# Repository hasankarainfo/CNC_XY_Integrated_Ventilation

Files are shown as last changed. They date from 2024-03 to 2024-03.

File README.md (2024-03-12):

# CNC_XY_Integrated_Ventilation
Diyot lazer uyumlu, bütünleşik havalandırmalı, iki eksen cnc.
<p align="center">
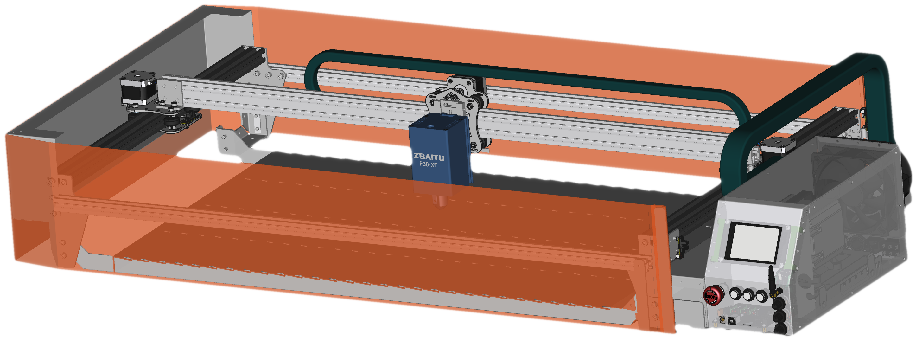
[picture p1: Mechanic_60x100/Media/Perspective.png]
    
</p>

Öne Çıkanlar:
1. Çalışması için, ihtiyaç duyduğu tüm materyalleri bütün olarak üzerinde barındırması,
2. Üzerinde bütünleşik bulunan ızgara ile, hava akımı yönlendirilmesi yanısıra, bal peteği ihtiyacının karşılanması,
3. Parça aydınlatma şiddeti, Havalandırma akış hızı, kompresör hava akış hız kontrolcüleri bulunması,
4. Tüm elektronik kontrolcülerin manuel ve ayrık yönetilmesi yanısıra, operasyonla birlikte de otomatik olarak bütünleşik çalışabilmesi,
5. Standart çalışma masası üzerinde, güç soketi ve havalandırma borusu takılmasına takriben kullanıma hazır olması,
6. Üretime uygunluğu ve mekanik dayanımı

Mekanik tasarımlar için FreeCad, Elektronik tasarımlar için ise Kicad, tamamen ücretsiz tasarım programları kullanılarak gerçekleştirildi.
<p align="left">
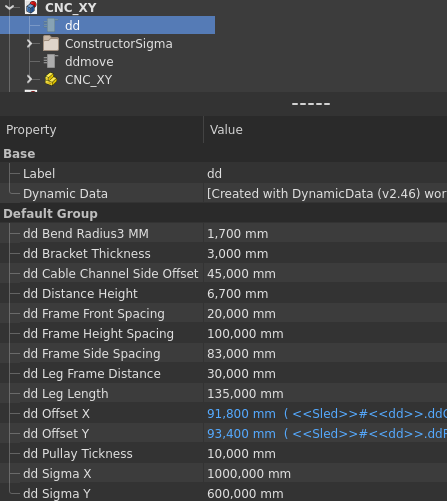
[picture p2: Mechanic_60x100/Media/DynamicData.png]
    
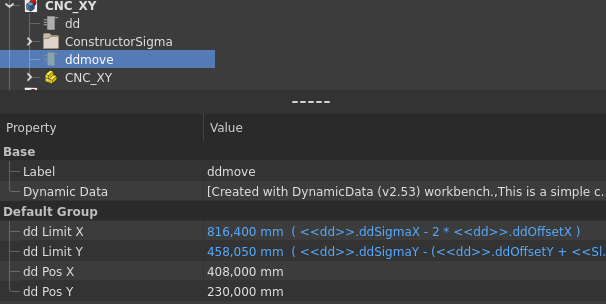
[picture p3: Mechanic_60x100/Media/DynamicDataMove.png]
    
</p>
CNC Mekanik boyutlar CNC_XY.FCStd dosyası ana sekmede dd (dynamic data) içerisinde ddSigmaX ve ddSigmaY değişkenleri üzerinden güncellenebilmektedir.
Bu değişkenler tasarımda bulunan x ve y eksenlerinde ki sigma profillerin birebir boylarına eştir. Sigma boylarına bağlı olan tüm parçalar otomatik güncellenecektir.
Bu durumda dikkat edilmesi gereken husus, büküm yapılacak metal parçalarda değişiklik meydana geldiğinge, üretime ilişkin  lazer kesim ve büküm rehberleri,
"./pr_.." dosyaları da ayrıca açılarak el ile güncellenmelidir. 3 boyutlu parçanın lazer kesime ve büküm rehberine uygunluğu için, 
yeniden "unfold" işlemi gerçekleştirilir. Yeniden meydana gelen kesim ve büküm eskiz'leri ilgili parçanın alanına sürüklenir. 
Teknik çizim dosyalarında, view sekmeleri içerisinde, ilişik olduğu eskiz ler, XSource properties üzerinden kesim ve büküm sıralaması ile güncellenir. 
Eski kesim ve büküm eskizleri silinebilir. Bazı durumda teknik çizimde ki ölçü belirteçleri de yeniden belirtilmesi gerekebilmektedir.

ddmove değişkenleri ile lazer hareket ettirilebilir. Sigma boyları ve diğer parametreler değerlendirilerek çalışma alanı otomatik hesaplanır, 
sonuç değerleri ddLimitX ddLimitY parametrelerinde görülür.

<p align="left">
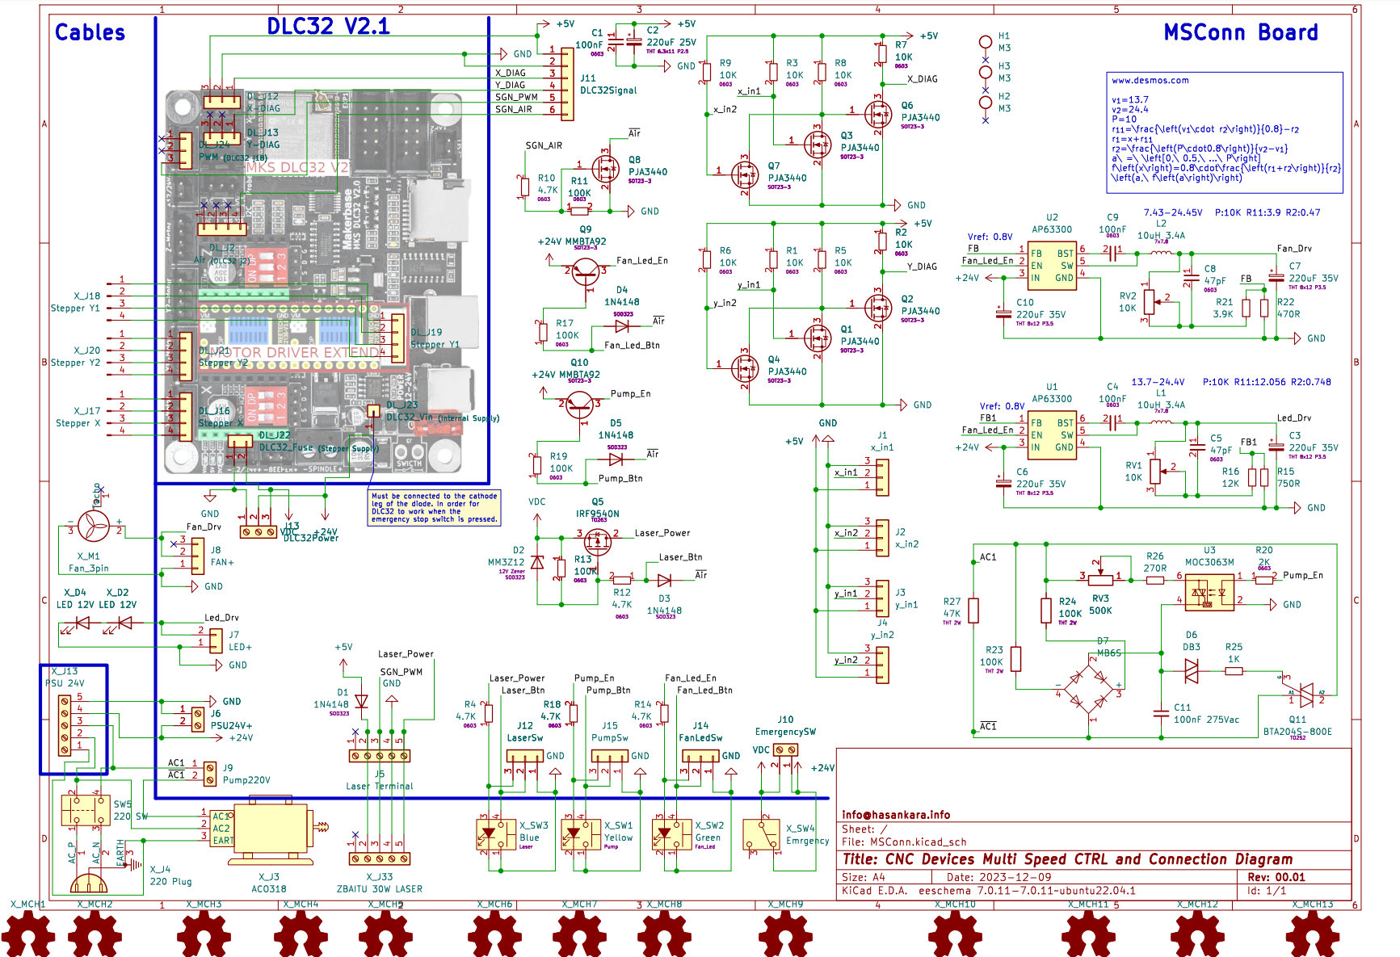
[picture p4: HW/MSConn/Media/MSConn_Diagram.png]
    
</p>
Elektriksel bağlantılar, Diyagram takip edilerek gerçekleştirilebilir. Diyagram MSConn board içerisinde tasarlandı, bu sayede kicad projesi üzerinden detaylı incelenebilir.
<p align="left">
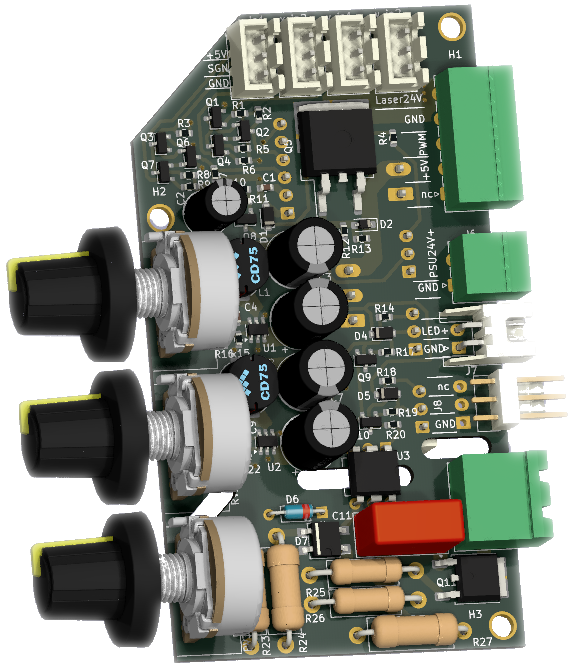
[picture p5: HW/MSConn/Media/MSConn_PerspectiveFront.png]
    
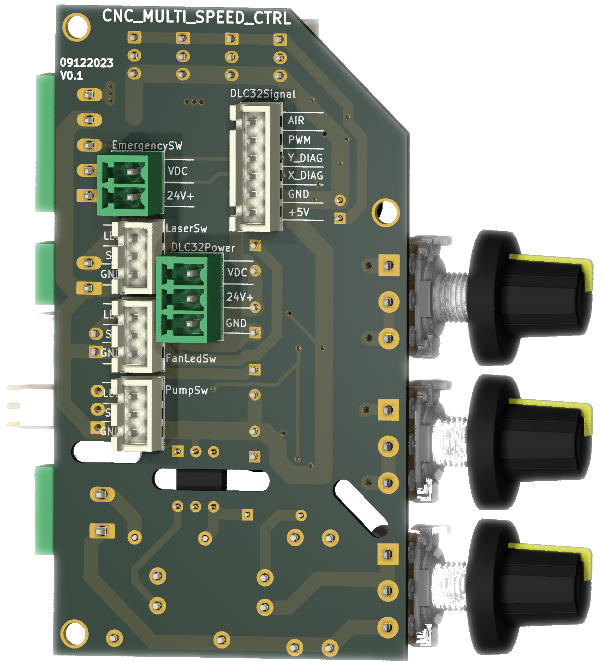
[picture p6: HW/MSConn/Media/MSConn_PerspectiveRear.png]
    
</p>

Üretim için öncelikle BOM dosyası incelenebilir.
Satın alınması gerekli materyallerin, satın alma linkleri ve yaklaşık fiyatlandırmaları Dolar cinsinde görülebilir.
1. sayfada genel toplam ve alt sayfaların sonuç fiyatlandırmaları görülmektedir.
2. sayfada Aygıt kutusu içerisinde kullanılan satın alınması gerekli parçalar görülmektedir.
3. sayfada satın alınması gerekli mekanik parçalar görülmektedir.
4. sayfada Projeye özgün metal parçaların üretilmesi için metal kesim, metal büküm listesi görülmektedir. 
    Dosya isimlerinden, metal kesimde kullanılacak materyalin cinsi ve kalınlığı anlaşılmaktadır.
    İhtiyaç duyulan kesim dosyaları, büküm rehberleri ve diş açma rehberleri "./Mechanic_60x100/Production_.." klasörlerinde bulunabilir.
5. sayfada "Multi Speed Controller and Connections" kartının üretiminde kullanılacak elektronik komponentlerin listesi bulunmaktadır.
    PCB üretiminde ihtiyaç duyulacak gerber dosyası "./HW/MSConn/FabOut_MSConn.zip" bulunabilir. 
    PCB Prototiplemede kullanılmak üzere detaylı MSConn bom listesi "./HW/MSConn/bom/ibom_MSConn.html"bulunabilir.
    Kart üzerinde konnektör pin isimleri anlamları ile birlikte yazmaktadır.

"./Mechanic_60x100/Media/" içerisinde ilk prototip montajına ilişkin fotoğraflar yer almaktadır. İlk prototip montaj esnasında,
görülen eksiklikler doğrultusunda, mekanik ve donanım tasarımlarında, gerekli görülen güncellemeler uygulanmıştır.

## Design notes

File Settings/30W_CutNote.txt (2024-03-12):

5mm mdf cut                         8mm focus 1 pass 250 speed, 100 power
5mm mdf, hardwood 45deg cut         8mm focus 1 pass 120 speed, 100 power
3mm translucent brown plexi cut     8mm focus 2 pass 220 speed, 100 power
3mm corrugated cardboard cutting    8mm focus 1 pass 4000 speed, 100 power

offset value 0.4mm. Used for complete overlap in cuts

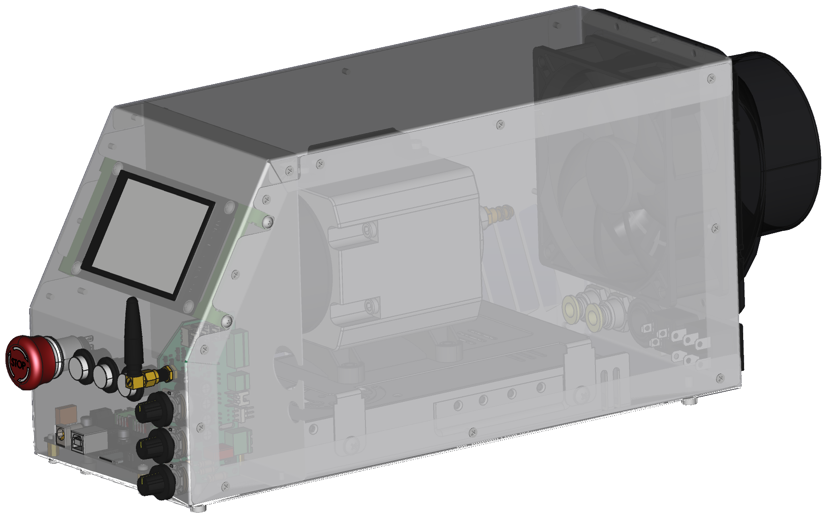
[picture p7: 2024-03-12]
Mechanic_60x100/Media/DevicesPerspective.png

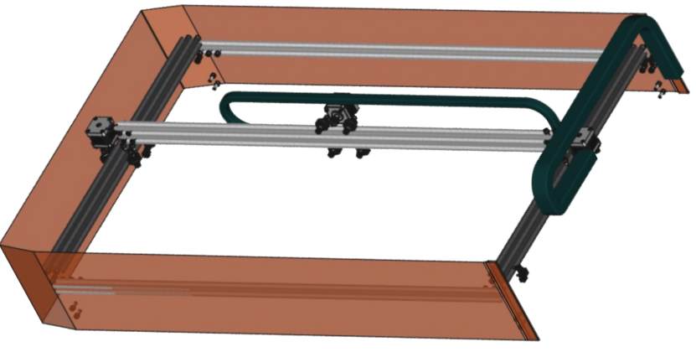
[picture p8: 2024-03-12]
Mechanic_60x100/Media/MechanicPerspective.png

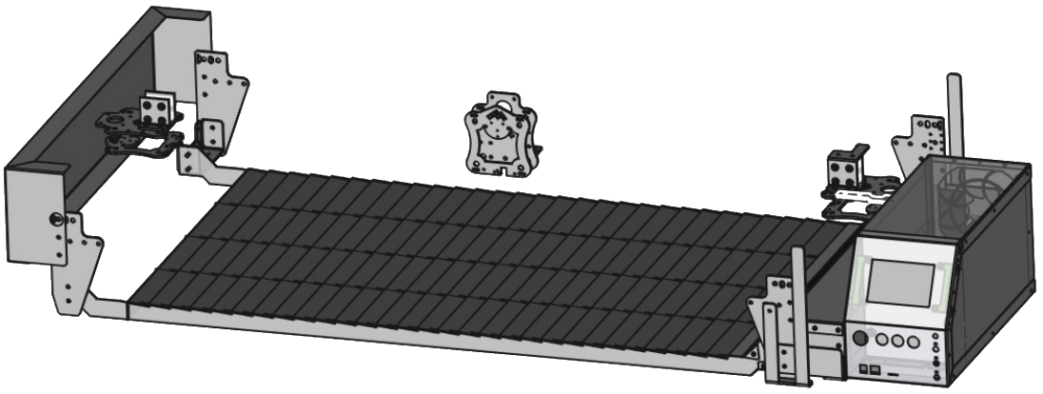
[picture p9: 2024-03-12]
Mechanic_60x100/Media/MetalProducedPerspective.png

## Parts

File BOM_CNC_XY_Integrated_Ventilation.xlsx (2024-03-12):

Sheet: Total
Reference | Value | Part Link | Part Number | Price | Qty
Laser | ZBAITU 30W LASER ~Price |  |  | 900 | 1 | 900.00
Devices Box Parts |  |  |  |  |  | 191.42
Mechanic Parts |  |  |  |  |  | 191.00
Metal Produced |  |  |  |  |  | 200.00
Grand Total |  |  |  |  |  | 1482.42

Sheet: Devices Box Parts
Reference | Value | Part Link | Part Number | Price | Qty
X_MCH7 | MKS DLC32 v2 | https://tr.aliexpress.com/item/1005005163045000.html | Suite 8 | 46 | 1 | 46.00
X_MCH8 | Air Flange 100mm | https://tr.aliexpress.com/item/1005005029283989.html | Color A | 6.7 | 1 | 6.70
X_MCH11 | Gland PG-13,5 | https://www.motorobit.com/pg-135-6-12-mm-polyamid-rakoru | OTO.SKP.02.000013 | 0.12 | 1 | 0.12
X_MCH12 | 2* Bulkhead Union 10mm | https://www.hidrofark.com/10-mm-perde-gecis-nipeli-pm-10 | PM-10 | 5 | 1 | 5.00
X_J3 | ACO318 | https://www.amazon.com.tr/gp/product/B00BNSQ16K/ref=ppx_yo_dt_b_asin_title_o00_s00 | ACO318 | 51 | 1 | 51.00
X_J4 | 220 Plug | https://www.motorobit.com/erkek-power-soketi-ic-212b | KOM.KNN.03.000014 | 0.25 | 1 | 0.25
X_J13 | PSU 24V | https://www.hatfon.com/urun/meanwell-lrs-350-24-350w-24v-14-6a-spms-guc-kaynagi | Lrs-350-24 | 35 | 1 | 35.00
X_M1 | Fan_3pin | https://www.perpaotomasyon.com/urun/krafe-120x120x38-24v-dc-turbo-fan | KF12038D24HB | 12 | 1 | 12.00
X_SW1 | Yellow | https://www.motorobit.com/rl16-503a-16mm-plastik-4-pin-kalici-buton-sari | BTN.PSH.01.000155 | 0.58 | 1 | 0.58
X_SW2 | Green | https://www.motorobit.com/rl16-503a-16mm-plastik-4-pin-kalici-buton-yesil | BTN.PSH.01.000154 | 0.58 | 1 | 0.58
X_SW3 | Blue | https://www.motorobit.com/rl16-503b-16mm-plastik-4-pin-yayli-buton-mavi | BTN.PSH.01.000161 | 0.58 | 1 | 12.00
X_SW4 | Emrgency | https://www.motorobit.com/19m-q1-19mm-metal-acil-stop-butonu | BTN.MTL.01.000419 | 6.8 | 1 | 11.60
SW5 | 220 SW | https://www.motorobit.com/kcd4-su-gecirmez-isikli-on-off-anahtar-4-pin | BTN.ROC.01.000020 | 1 | 1 | 0.01
MSConn |  |  |  |  |  | 10.58
Total |  |  |  |  |  | 191.42

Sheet: Mechanic Parts
Reference | Value | Part Link | Part Number | Price | Qty
X_D2, X_D4 | LED 12V + 12V |  | CT-4538 | 6.5 | 1 | 6.50
X_J17, X_J18, X_J20 | -- mixed values -- | https://www.rhino3dprinter.com/urun/nema-17-step-motor-nema17 | rhn-513249 | 11 | 3 | 33.00
X_MCH2 | 12x V Wheel | https://www.rhino3dprinter.com/urun/v-slot-tekerlek/239 | 47944814 | 12 | 1 | 12.00
X_MCH3 | 6x 6mm Eccentric Nut Group | https://www.rhino3dprinter.com/urun/eksantrik-somun/713 | RHN-511474 | 11.6 | 1 | 11.60
X_MCH4 | 3M Strap | https://www.rhino3dprinter.com/urun/kaliteli-gt2-6mm-kaucuk-kayis/4470 | RHN-523002 | 8.5 | 1 | 8.50
X_MCH5 | 3x GT2 Pulley 20Teeth | https://www.rhino3dprinter.com/urun/gt2-kasnak-20-dis-5mm/1096 | rhn-510705 | 2.8 | 1 | 2.80
X_MCH6 | 4x Optic Limit SW | https://www.motorobit.com/3d-yazici-optik-limit-switch-endstop | 3DP.3DE.01.000015 | 5 | 1 | 5.00
X_MCH9 | 102MM - 5 M PVC Air Duct | https://www.toprakvesu.com/afs-yirtilmaz-pvc-hava-kanali-102-mm | LB003 | 15.3 | 1 | 15.30
X_MCH10 | 3M Transparent Orange PVC Tarpaulin | https://www.kumasci.com/urun/seffaf-branda-pvc-mika-0,60-mm-turuncu-renkli-137-cm-en/5457 | KM-5457 | 21 | 1 | 21.00
X_MCH13 | 12mm 1M Cable Sock | https://www.rhino3dprinter.com/urun/12mm-siyah-kablo-corabi/3859 | RHN-514802 | 0.8 | 1 | 0.80
X_MCH14 | 1M 18x25 Cable Carrier | https://www.parsrulman.com/18x25-kablo-tasiyici-kapali/ | 18X25 | 10 | 1 | 10.00
X_MCH15 | 2M 10x10 Cable Carrier | https://www.parsrulman.com/10x10-kablo-tasiyici/ | 10x10 | 13 | 1 | 13.00
X_MCH16 | 2*60 1*100cm V_Sigma_40x20 | https://www.rhino3dprinter.com/urun/v-slot-20x40-siyah-sigma-profil | RHN-504520 | 33.5 | 1 | 33.50
X_MCH17 | 2*100cm Sigma_20x20 | https://www.rhino3dprinter.com/urun/sigma-profil-gri-renk-20x20 | RHN-516882 | 18 | 1 | 18.00
Total |  |  |  |  |  | 191.00

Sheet: Metal Produced
Reference | Part Link | Price
1.5mm aluminium cut
3mm aluminium cut
2mm Stainless steel cut
0.8mm Steel cut
2mm Steel cut
3mm Steel cut
Abkant Press Process
Mechanical Post Process
Total ~ |  |  | 200

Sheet: MSConn
Reference | Value | Pad | Part Link | Part Number | Price | Qty
C1, C4, C9 | 100nF | 603 | https://ozdisan.com/Product/Detail/476015/CC0603KRX7R9BB104 | CC0603KRX7R9BB104 | 0.006 | 3 | 0.02
C2 | 220uF 25V | THT 6.3x11 P2.5 | https://ozdisan.com/Product/Detail/404352/TMP221M1EE11M | TMP221M1EE11M | 0.06 | 1 | 0.06
C3, C6, C7, C10 | 220uF 35V | THT 8x12 P3.5 | https://ozdisan.com/Product/Detail/593553/JRB1V221M05000800120000A | JRB1V221M05000800120000A | 0.04 | 4 | 0.16
C5, C8 | 47pF | 603 | https://ozdisan.com/Product/Detail/747244/CC0603JRNPO9BN470 | CC0603JRNPO9BN470 | 0.006 | 2 | 0.01
C11 | 100nF 275Vac |  | https://ozdisan.com/Product/Detail/605274/W42Q3104KK6SD1A0W1 | W42Q3104KK6SD1A0W1 | 0.05 | 1 | 0.05
D1, D3-D5 | 1N4148 | SOD323 | https://ozdisan.com/Product/Detail/453557/1N4148WS-HT | 1N4148WS-HT | 0.014 | 4 | 0.06
D2 | MM3Z12 | SOD323 | https://ozdisan.com/Product/Detail/581368/MM3Z12-HT | MM3Z12-HT | 0.025 | 1 | 0.03
D6 | DB3 |  | https://www.ozdisan.com/Product/Detail/27193/DB3 | DB3 | 0.07 | 1 | 0.07
D7 | MB6S |  | https://ozdisan.com/Product/Detail/467250/MB6S-0-5A-HT | MB6S-0.5A-HT | 0.036 | 1 | 0.04
J1-J4, J12, J14, J15 | -- mixed values -- |  | https://www.ozdisan.com/Product/Detail/493781/DS1066-3MVW6X | DS1066-3MVW6X | 0.015 | 7 | 0.10
J5 | Laser Terminal |  | https://www.ozdisan.com/Product/Detail/353433/15EDGRC-3-5-05P-14-00SH | 15EDGRC-3.5-05P-14-00SH | 0.13 | 1 | 0.13
J6 | PSU24V+ |  | https://www.ozdisan.com/Product/Detail/424780/15EGTRC-3-5-02P-14-00AH | 15EGTRC-3.5-02P-14-00AH | 0.06 | 1 | 0.06
J7 | LED+ |  | https://www.ozdisan.com/Product/Detail/347995/DS1069-2MRW6SA | DS1069-2MRW6SA | 0.01 | 1 | 0.01
J8 | FAN+ |  | https://www.ozdisan.com/Product/Detail/458356/L-KLS1-2-54-03-R | L-KLS1-2.54-03-R | 0.03 | 1 | 0.03
J9 | Pump220V |  | https://www.ozdisan.com/Product/Detail/701614/2EGTRC-5-0-02P-14-00AH | 2EGTRC-5.0-02P-14-00AH | 0.06 | 1 | 0.06
J10 | EmergencySW |  | https://www.ozdisan.com/Product/Detail/707708/15EDGVC-3-5-02P-12-00AH | 15EDGVC-3.5-02P-12-00AH | 0.09 | 1 | 0.09
J11 | DLC32Signal |  | https://www.ozdisan.com/Product/Detail/348001/DS1069-6MVW6X | DS1069-6MVW6X | 0.03 | 1 | 0.03
J13 | DLC32Power |  | https://www.ozdisan.com/Product/Detail/701062/15EDGVC-3-5-03P-14-00AH | 15EDGVC-3.5-03P-14-00AH | 0.1 | 1 | 0.10
L1, L2 | 10uH 3.4A | 7x7.8 | https://ozdisan.com/Product/Detail/527917/FPI0705-100M | FPI0705-100M | 0.2 | 2 | 0.40
Q1-Q4, Q6-Q8 | PJA3440 | SOT23-3 | https://ozdisan.com/Product/Detail/517995/PJA3440R200001 | PJA3440_R2_00001 | 0.1 | 7 | 0.70
Q5 | IRF9540N | TO263 | https://ozdisan.com/Product/Detail/612326/IRF9540NSTRLPBF | IRF9540NSTRLPBF | 0.9 | 1 | 0.90
Q9, Q10 | MMBTA92 | SOT23-3 | https://ozdisan.com/Product/Detail/433898/MMBTA92-HT | MMBTA92-HT | 0.03 | 2 | 0.06
Q11 | BTA204S-800E | TO252 | https://ozdisan.com/Product/Detail/981895/BTA204S-800E118 | BTA204S-800E,118 | 0.34 | 1 | 0.34
R1-R3, R5-R9 | 10K | 603 | https://ozdisan.com/Product/Detail/341790/0603SAF1002T5E | 0603SAF1002T5E | 0.0015 | 8 | 0.01
R4, R10, R12, R14, R18 | 4.7K | 603 | https://ozdisan.com/Product/Detail/341796/0603SAF4701T5E | 0603SAF4701T5E | 0.0015 | 5 | 0.01
R11, R13, R17, R19 | 100K | 603 | https://ozdisan.com/Product/Detail/339374/0603SAF1003T5E | 0603SAF1003T5E | 0.0015 | 4 | 0.01
R15 | 750R |  | https://ozdisan.com/Product/Detail/344357/0603SAF7500T5E | 0603SAF7500T5E | 0.001 | 1 | 0.001
R16 | 12K |  | https://ozdisan.com/Product/Detail/353308/0603SAF1202T5E | 0603SAF1202T5E | 0.001 | 1 | 0.001
R20 | 2K | 603 | https://ozdisan.com/Product/Detail/347334/0603SAF2001T5E | 0603SAF2001T5E | 0.0015 | 1 | 0.0015
R21 | 3.9K |  | https://ozdisan.com/Product/Detail/357181/0603SAF3901T5E | 0603SAF3901T5E | 0.001 | 1 | 0.001
R22 | 470R |  | https://ozdisan.com/Product/Detail/348835/0603SAF4700T5E | 0603SAF4700T5E | 0.001 | 1 | 0.001
R23, R24 | 100K | THT 2W | https://www.ozdisan.com/Product/Detail/866960/CFR2WSJT-52-100K | CFR2WSJT-52-100K | 0.05 | 2 | 0.10
R25 | 1K |  | https://www.ozdisan.com/Product/Detail/904507/MFR-25FTE52-1K | MFR-25FTE52-1K | 0.015 | 1 | 0.01
R26 | 270R |  | https://www.ozdisan.com/Product/Detail/905436/MFR-25FTF52-270R | MFR-25FTF52-270R | 0.015 | 1 | 0.01
R27 | 47K | THT 2W | https://www.ozdisan.com/Product/Detail/867440/CFR3WSJT-73-47K | CFR3WSJT-73-47K | 0.06 | 1 | 0.06
RV1, RV2 | 10K |  | https://www.entegredunyasi.com.tr/urun/10k-mavi-potans | WH0162-10K POTANS | 0.84 | 2 | 1.68
RV3 | 500K |  | https://www.entegredunyasi.com.tr/urun/500k-mavi-potansiyometre-wh0162-500k | WH0162-500K POTANS | 0.84 | 1 | 0.84
U1, U2 | AP63300 |  | https://www.digikey.com/en/products/detail/diodes-incorporated/AP63300WU-7/10491510 | 31-AP63300WU-7CT-ND | 0.82 | 2 | 1.64
U3 | MOC3063M |  | https://ozdisan.com/Product/Detail/337684/MOC3063M | MOC3063M | 0.7 | 1 | 0.70
X_MCH1 | PCB Produced |  | https://jlcpcb.com/ |  | 2 | 1 | 2.00
 |  |  |  |  |  |  | 0.00
Total |  |  |  |  |  |  | 10.58

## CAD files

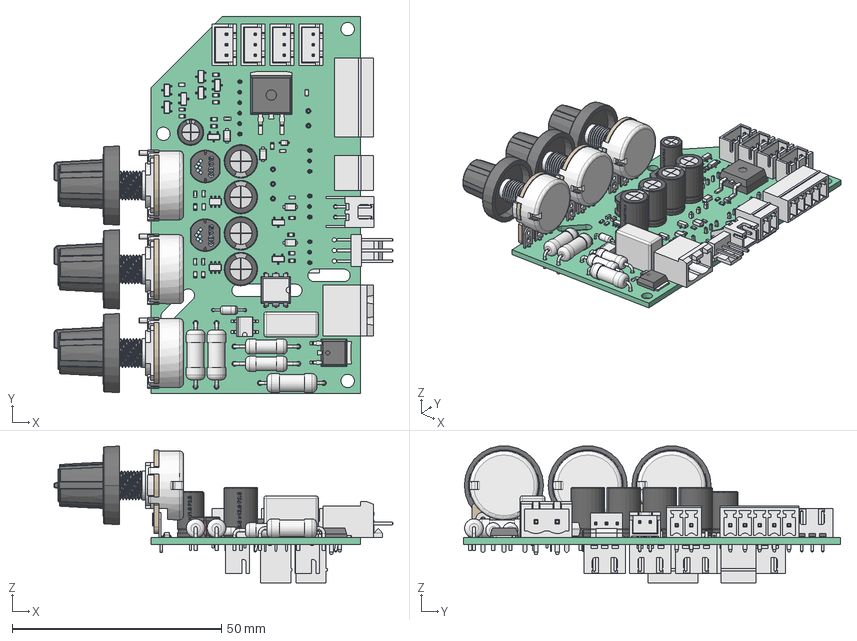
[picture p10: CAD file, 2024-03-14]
HW/MSConn/MSConn3D.FCStd
80.9 x 90.0 x 32.7 mm
Pcb_38e4
Knob_18.5 x 3
Mil x 3
pcb x 3
Pin3 x 3
Pin1 x 3
Pin2 x 3
Metal x 3
Q11_SOT_23_d14ee1c078b6 x 9
D7_D_SOD_323_dd79eabc5d6b
R15_R_0603_1608Metric_0c346f64d96a x 20
Sketch_On_Surface x 4
Sketch_On_Surface001 x 4
Sketch_On_Surface002 x 4
Sketch_On_Surface003 x 4
Sketch_On_Surface004 x 4
Sketch_On_Surface005 x 4
Sketch_On_Surface006 x 4
Sketch_On_Surface007 x 4
Sketch_On_Surface008 x 4
Sketch_On_Surface009 x 4
Sketch_On_Surface010 x 4
Sketch_On_Surface011 x 4
D8_TO-269AA_2bfa4c3bc879
C20_C_Rect_L130mm_W60mm_P1000mm_FKS3_FKP3_MKS4_719aee594432
D3_D_SOD_123F_0e6f75c736fe x 4
J15_JST_B3B_XH_A_ce7ef635c6d0 x 7
J29_MSTBA_01x02_G_5_08mm_e88b5a3cc893
C3_C_0603_1608Metric_60dfc148ec75 x 5
U5_TSOT_23_6_e728020bdb3d x 2
R22_R_Axial_DIN0414_L119mm_D45mm_P1524mm_Horizontal_7fed01040269 x 3
U6_DIP-6_W7.62mm_bc15a999cf1c
TextSolid x 2
TextSolid001 x 2
TextSolid002 x 2
TextSolid003 x 2
TextSolid004 x 2
TextSolid005 x 2
TextSolid006 x 2
TextSolid007 x 2
TextSolid008 x 2
TextSolid009 x 2
Pinouts_Fillet x 2
Pinouts_Fillet001 x 2
J27_JST_S2B_XH_A_f3c9ba6d6086
J31_MC_01x02_G_3_5mm_9bf914f047c8
J28_MC_01x05_G_3_5mm_ab80e944cf0b
J1_Fan_Pin_Header_Straight_1x03_85ed5d203a81
a3dd6ad7-9c39-11ed-93f0-dde97e994e83_part
a3dd6ad8-9c39-11ed-93f0-dde97e994e83_part
a3dd6ad9-9c39-11ed-93f0-dde97e994e83_part
a3dd6ad9-9c39-11ed-93f0-dde97e994e83_part001
a3dd6ad9-9c39-11ed-93f0-dde97e994e83_part002
R31_R_Axial_DIN0411_L99mm_D36mm_P1524mm_Horizontal_5a3f2440dadf x 2
Sketch_On_Surface013
Sketch_On_Surface014
Sketch_On_Surface015
Sketch_On_Surface016
Sketch_On_Surface017
Sketch_On_Surface018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

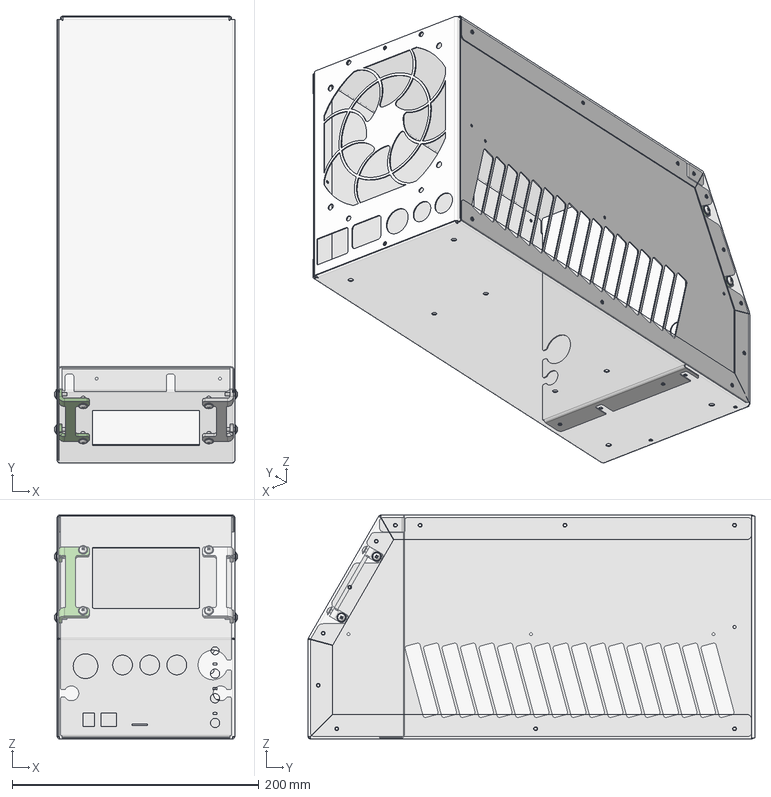
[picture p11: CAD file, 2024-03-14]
Mechanic_60x100/CNC_Devices.FCStd
148.8 x 362.4 x 181.6 mm
tft_screws_l x 2
tft_screws_local_l x 2
Fold
Frame_Side_L
Frame_Side_R
Frame_Rear
FrameSeperator
Frame_Main

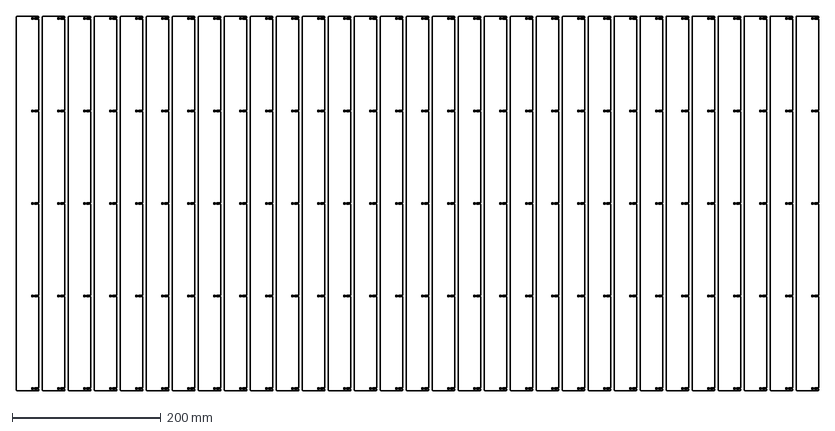
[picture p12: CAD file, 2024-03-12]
Mechanic_60x100/Production_LaserCut_Bending/Pr_Alu_1_5MM_LaserCut.dxf
1080.0 x 504.0 mm

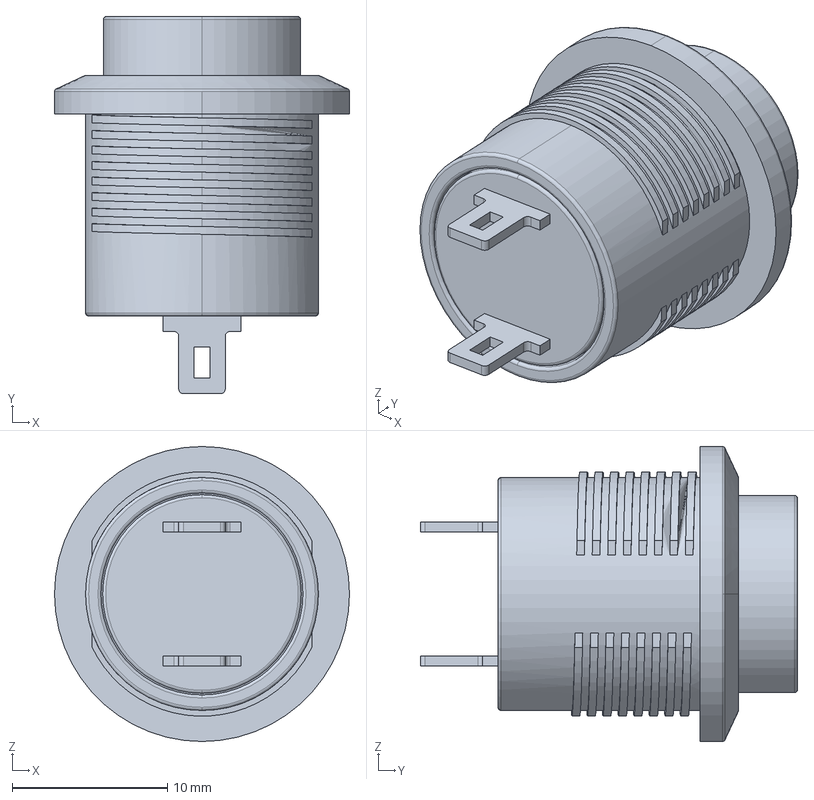
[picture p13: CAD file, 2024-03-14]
Mechanic_60x100/SubParts/Push_Button_D16.FCStd
19.0 x 24.3 x 19.0 mm

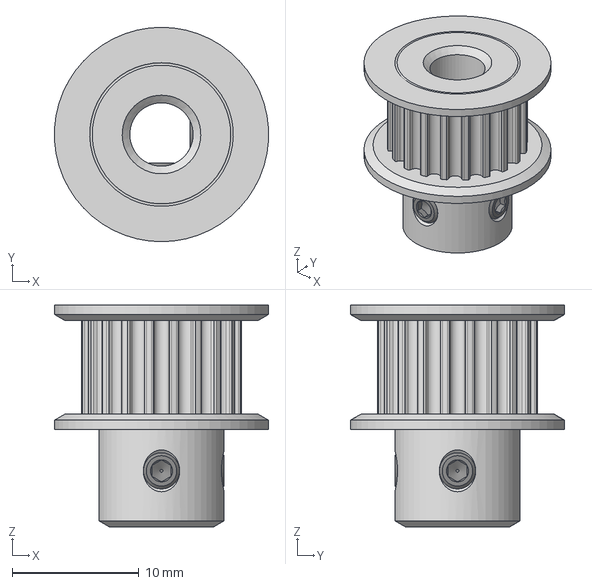
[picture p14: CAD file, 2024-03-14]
Mechanic_60x100/SubParts/Sled_SubParts/Pulley_GT_P.FCStd
16.9 x 16.9 x 17.5 mm
M3x2.6950000000000003-Screw x 2
CompoundFilter

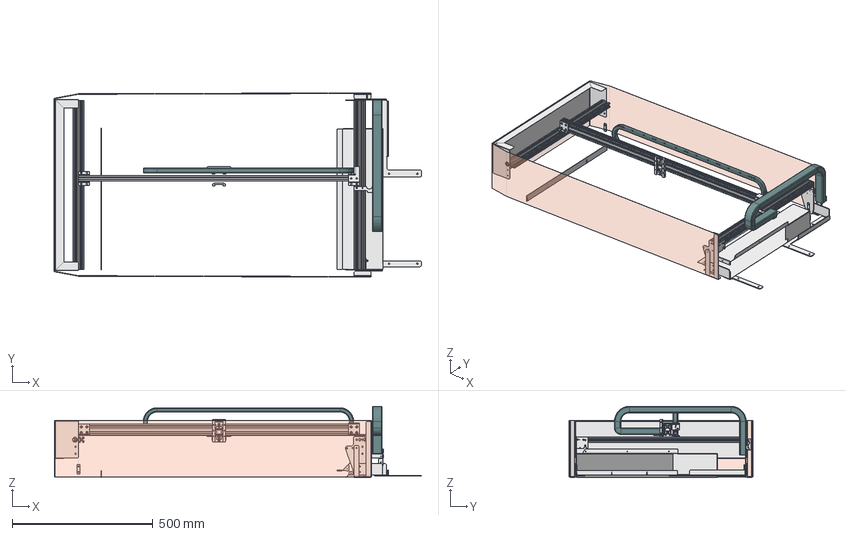
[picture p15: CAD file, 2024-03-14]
Mechanic_60x100/CNC_XY.FCStd
1305.3 x 653.5 x 253.6 mm
LaserElevator
SigmaMid4020
CompoundFilter003 x 4
CableChannelR
ExtrudeCableChannelSideHolder x 2
Slice009.0
SideGuard_
SigmaSide4020 x 2
TnutDouble x 2
LeftLimit
AirFrameTop
AirFrameBottom
CableChannelSidePlastic
Slice007.0
SensorMountF
M3x6xx5-Standoff
M3x6xx5-Standoff414
BaseBarrier
BaseBarrierHolderFront
BaseBarrierHolderRear
DeviceHolderF
DeviceHolderR
LegBaseRightFront
LegBaseRightRear

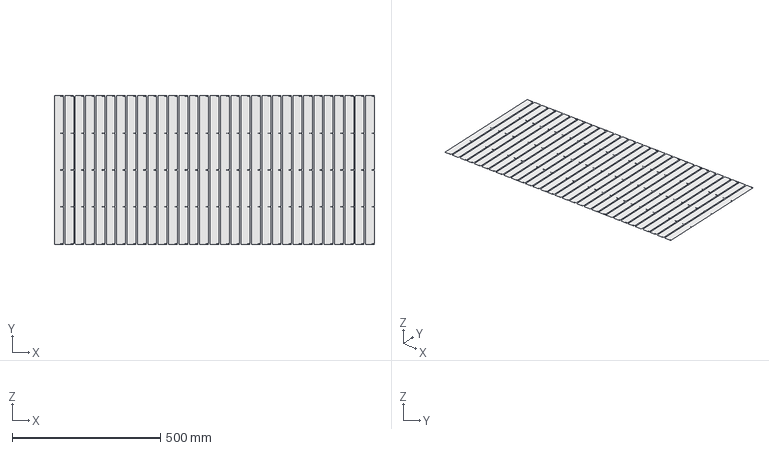
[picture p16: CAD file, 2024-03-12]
Mechanic_60x100/Production_LaserCut_Bending/Pr_Alu_1_5mm.FCStd
1080.0 x 504.0 x 0 mm

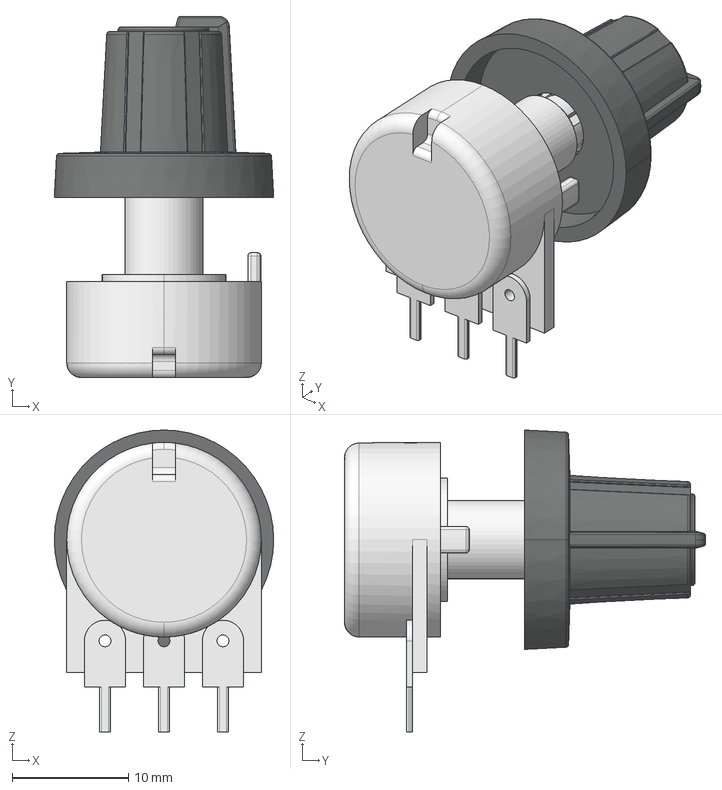
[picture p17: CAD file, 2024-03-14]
Mechanic_60x100/SubParts/Potentiometer_Mono.FCStd
18.9 x 31.1 x 26.0 mm
Knob_18.5
Potentiometer

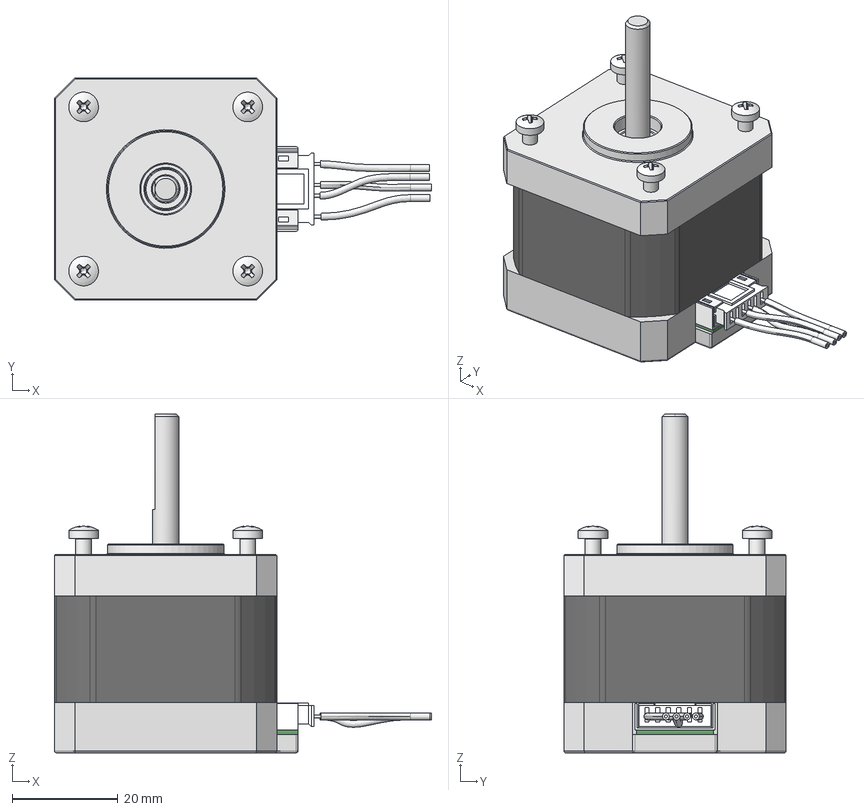
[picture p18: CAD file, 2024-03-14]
Mechanic_60x100/SubParts/Sled_SubParts/Nema_17HS4401_P.FCStd
71.2 x 42.0 x 64.0 mm
Axis&Rotor
BallBearing1
Stator_
Baseplate_
BallBearing1_
Seperate
PCB
ConnectorPins
ConnBase
Cables_Plastic
Cables_Cu_
Housing_Female__
FrontPlate
ScrewsBody
ScrewsAssembly

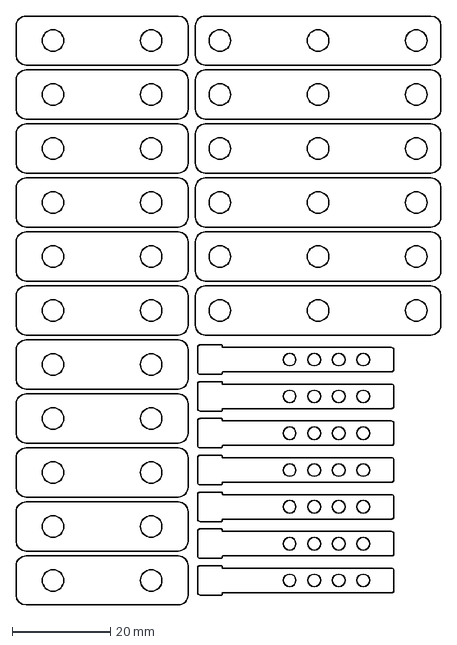
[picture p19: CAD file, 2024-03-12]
Mechanic_60x100/Production_LaserCut_Bending/Pr_StainlessSteel_2MM_LaserCut.DXF
86.5 x 120.0 mm

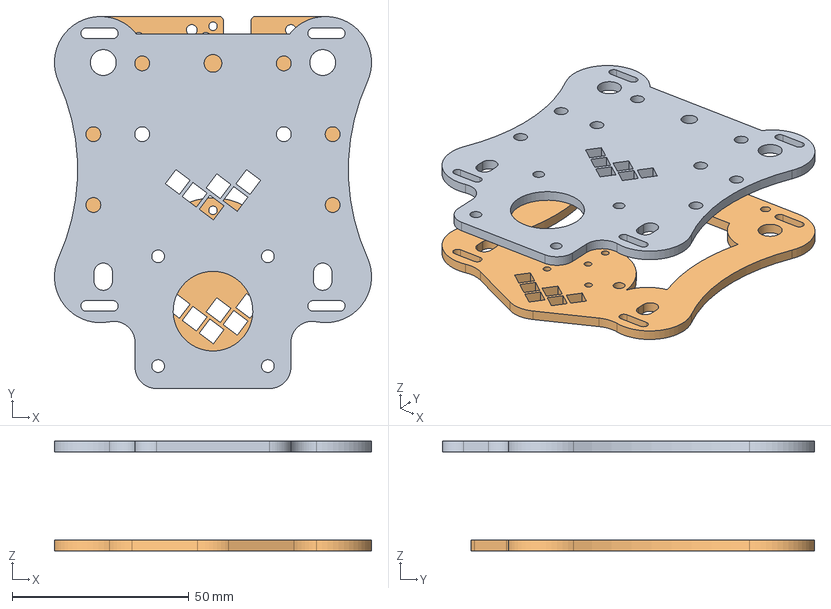
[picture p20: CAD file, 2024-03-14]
Mechanic_60x100/SubParts/Sled.FCStd
89.6 x 105.1 x 31.0 mm
Sled1
Sled2

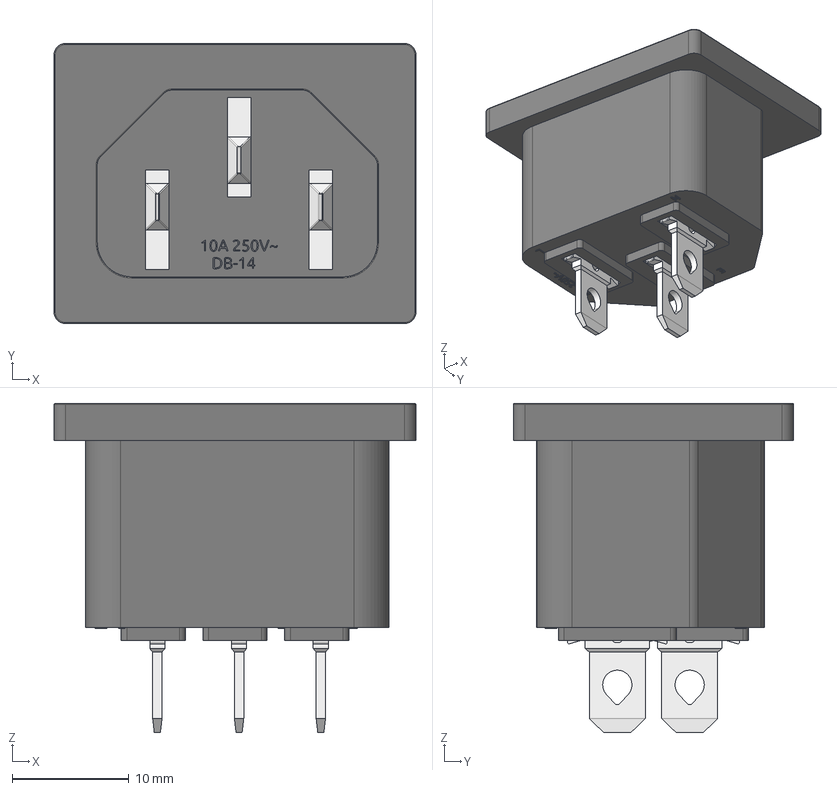
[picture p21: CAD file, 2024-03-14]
Mechanic_60x100/SubParts/IEC_Plug.FCStd
31.0 x 24.0 x 28.2 mm
MainBody
PinLeft x 2
PinMid

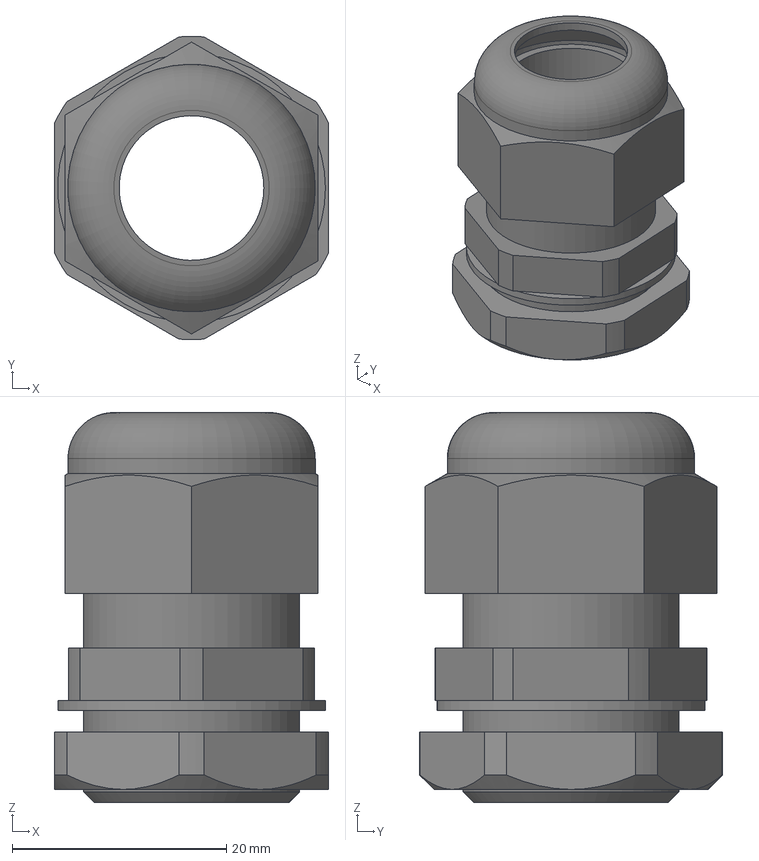
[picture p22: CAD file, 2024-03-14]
Mechanic_60x100/SubParts/PG13.5 Gland.FCStd
25.6 x 28.3 x 36.4 mm

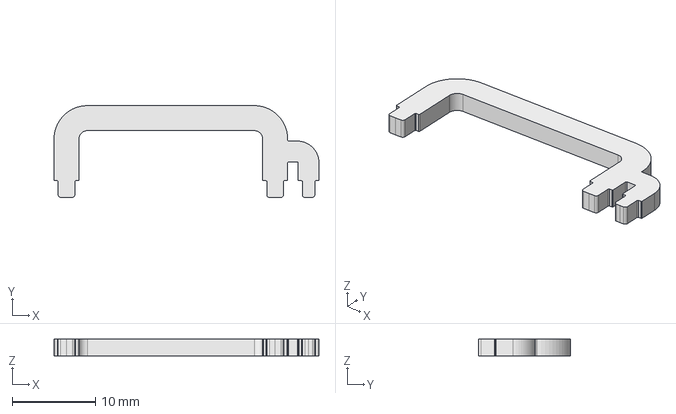
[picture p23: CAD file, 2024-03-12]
Mechanic_60x100/Production_LaserCut_Bending/BonusStainlessSHUNT.FCStd
31.8 x 11.0 x 2.00 mm

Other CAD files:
Mechanic_60x100/Production_MechanicalPostProcess/Pr_MechPost.FCStd
Mechanic_60x100/Production_LaserCut_Bending/Pr_Steel_2_0mm.FCStd
Mechanic_60x100/Production_LaserCut_Bending/Pr_Steel_3_0mm.FCStd
Mechanic_60x100/SubParts/Logo.FCStd
Mechanic_60x100/Production_LaserCut_Bending/Pr_Alu_3MM_LaserCut.dxf
Mechanic_60x100/Production_LaserCut_Bending/Pr_Alu_3_0mm.FCStd
Mechanic_60x100/Production_LaserCut_Bending/Pr_StainlessSteel_2_0mm.FCStd
Mechanic_60x100/Production_LaserCut_Bending/Pr_Steel_0_8MM_LaserCut.dxf
Mechanic_60x100/Production_LaserCut_Bending/Pr_Steel_0_8mm.FCStd
Mechanic_60x100/Production_LaserCut_Bending/Pr_Steel_2MM_LaserCut.dxf
Mechanic_60x100/Production_LaserCut_Bending/Pr_Steel_3MM_LaserCut.dxf
Mechanic_60x100/SubParts/Bulkhead_Union_BQ-BU10.FCStd
Mechanic_60x100/SubParts/EmergencyStopButton.FCStd
Mechanic_60x100/SubParts/F30-XF.FCStd
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

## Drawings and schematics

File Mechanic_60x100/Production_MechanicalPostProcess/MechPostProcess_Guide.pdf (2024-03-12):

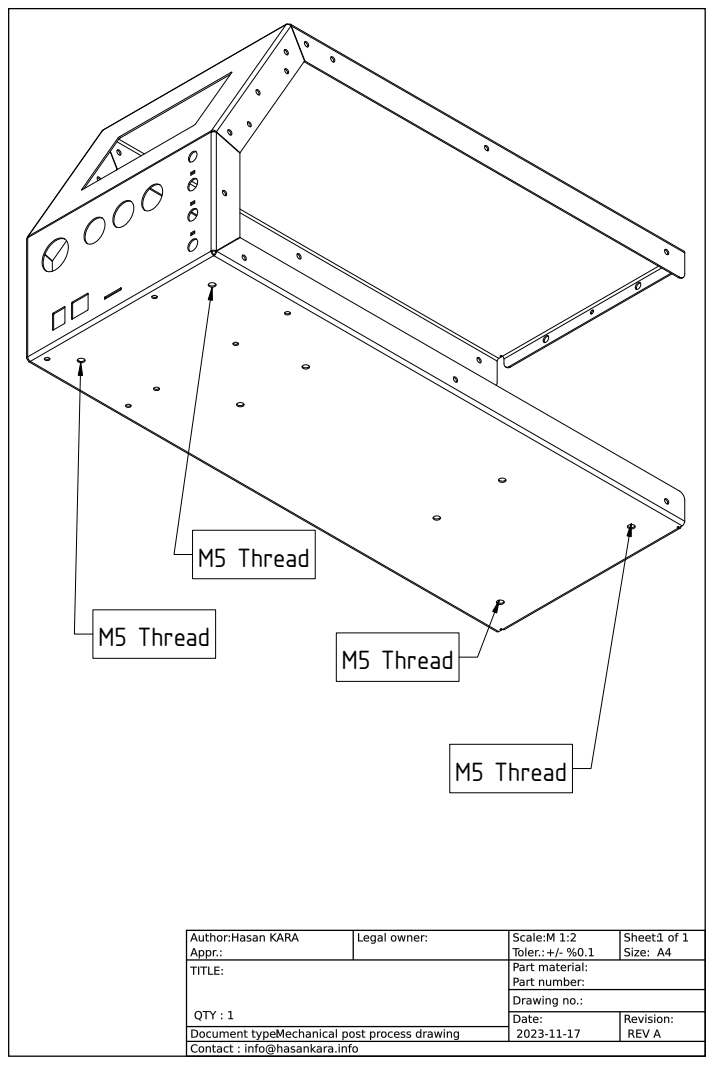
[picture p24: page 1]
M5 Thread

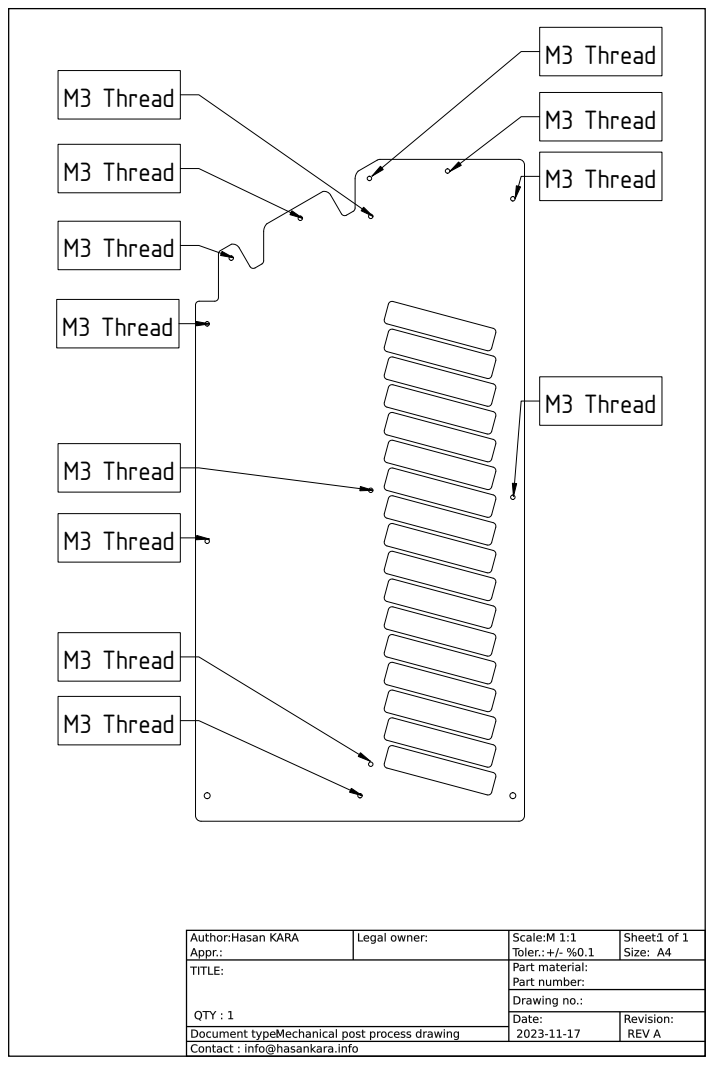
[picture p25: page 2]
hre

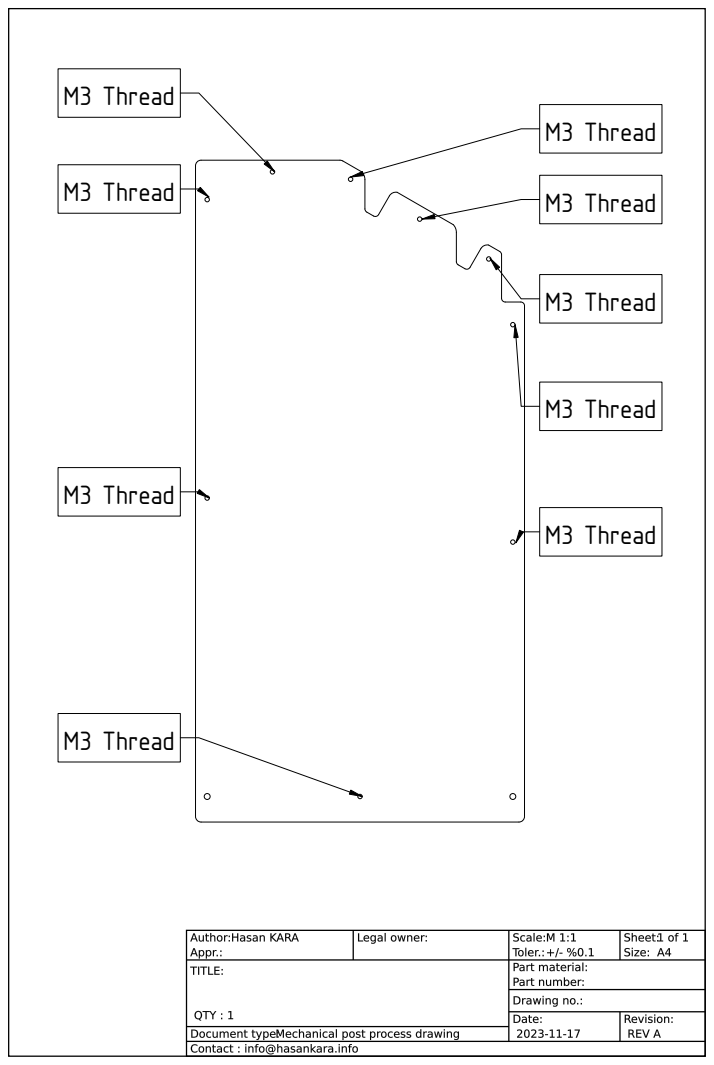
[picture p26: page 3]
M3 Thread

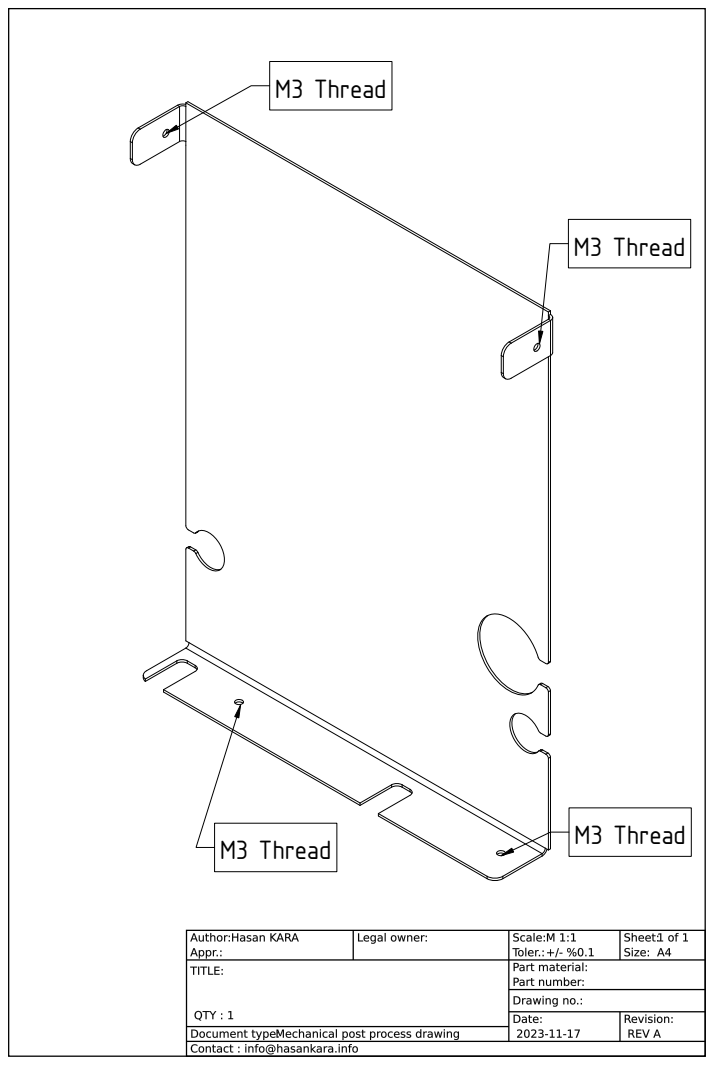
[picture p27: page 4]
M3 Thread; M3 Thread M3 Thread

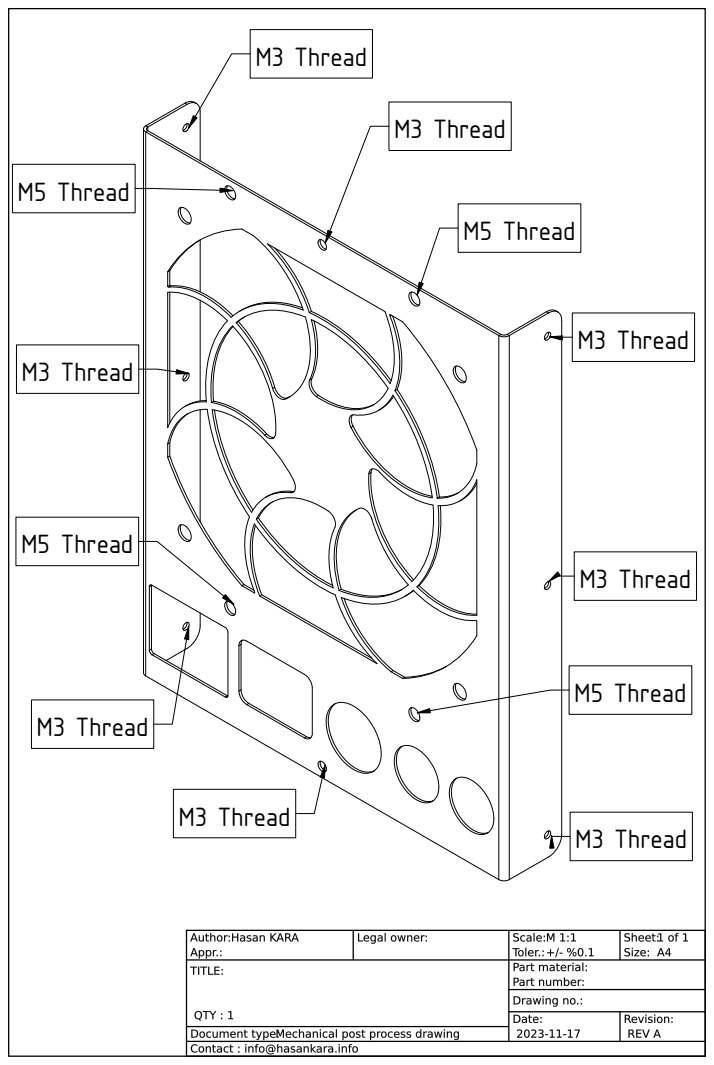
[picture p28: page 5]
M3 Thread; M5 Thread

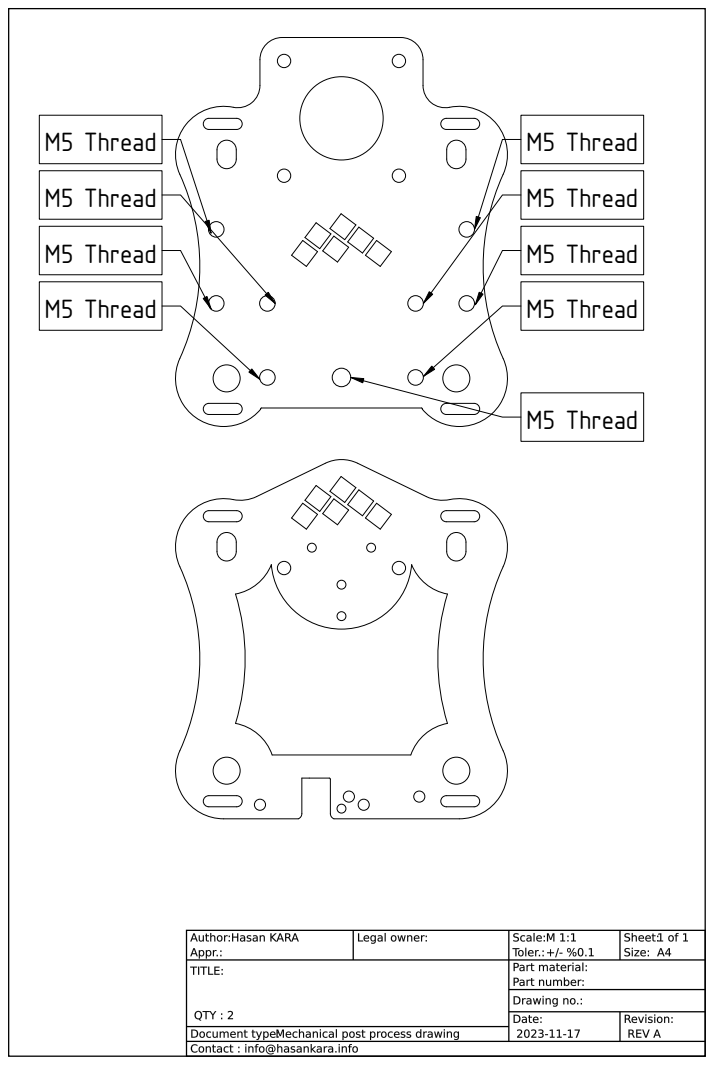
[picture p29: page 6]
hre

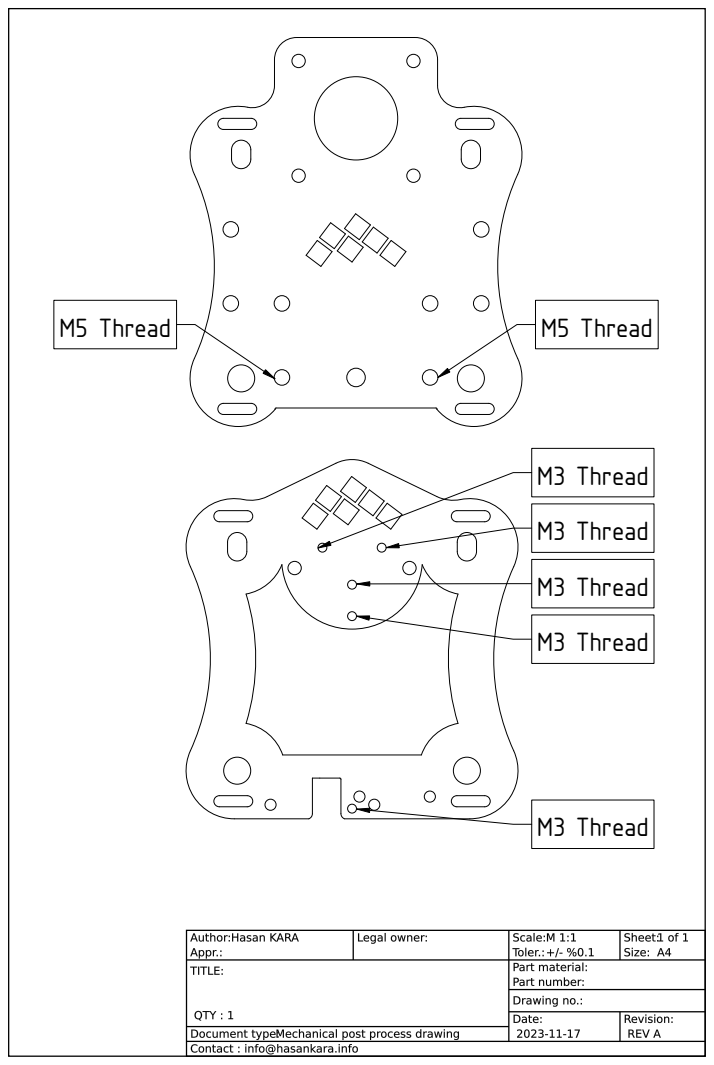
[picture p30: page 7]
M5 Thread; M3 Thread M3 Thread M3 Thread; M3 Thread

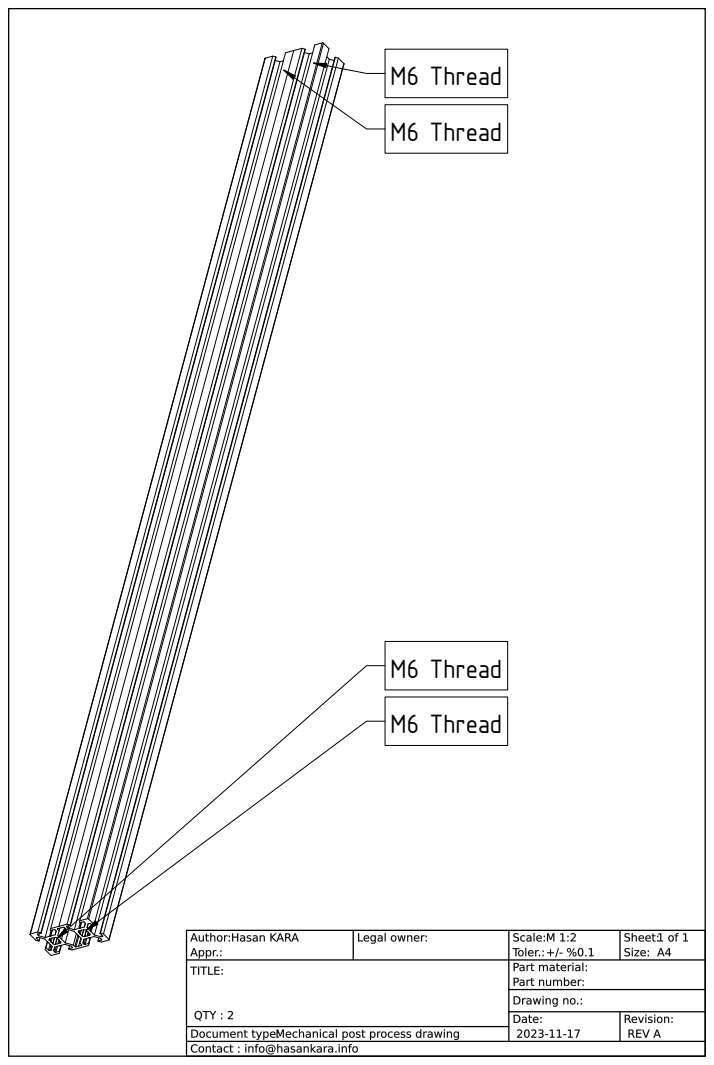
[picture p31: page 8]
M6 Thread

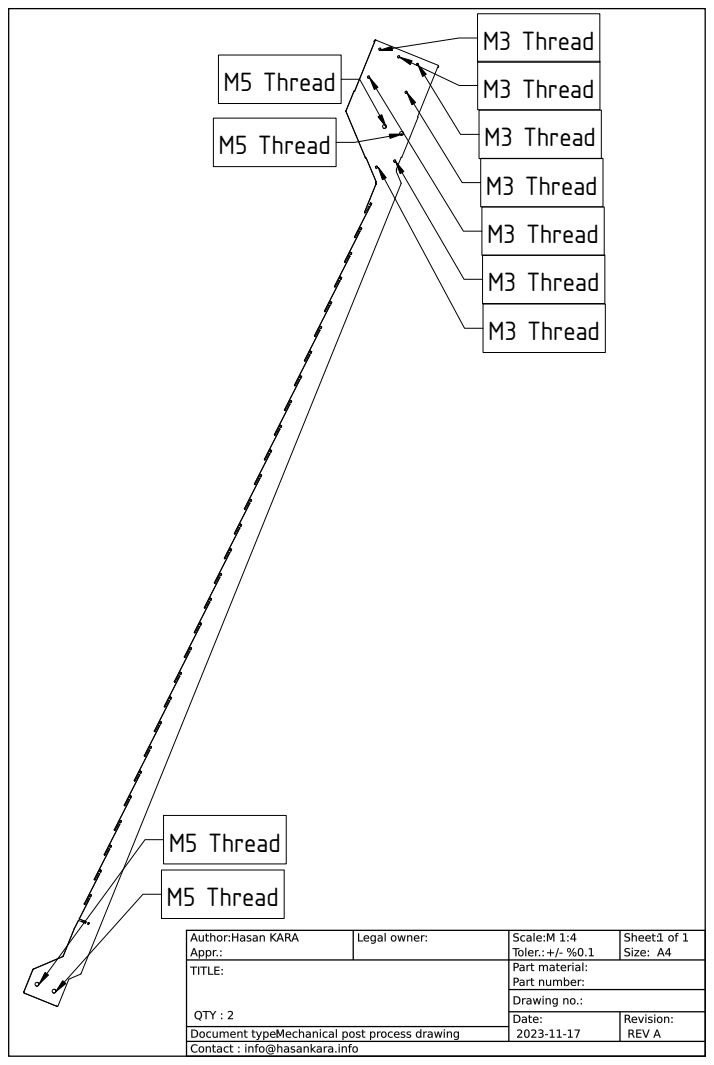
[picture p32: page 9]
M5 Thread; M3 Thread; M3 Thread M3 Thread

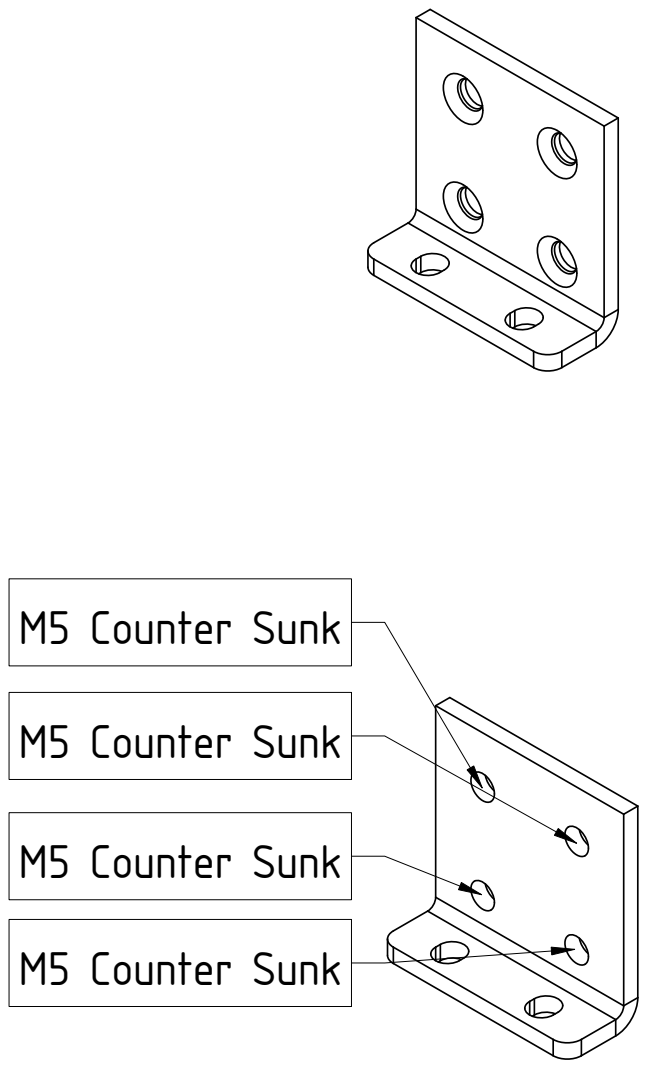
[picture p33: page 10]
M5 Counter Sunk

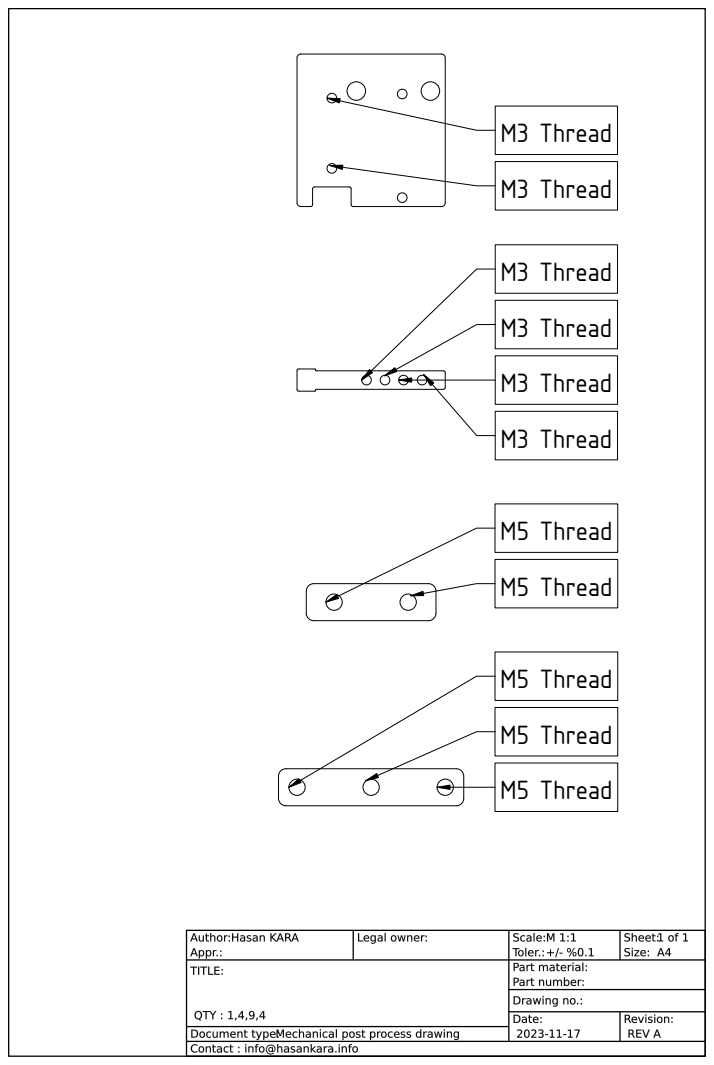
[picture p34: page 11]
M3 Thread M3 Thread; M3 Thread M3 Thread M3 Thread M3 Thread; M5 Thread M5 Thread; M5 Thread M5 Thread M5 Thread

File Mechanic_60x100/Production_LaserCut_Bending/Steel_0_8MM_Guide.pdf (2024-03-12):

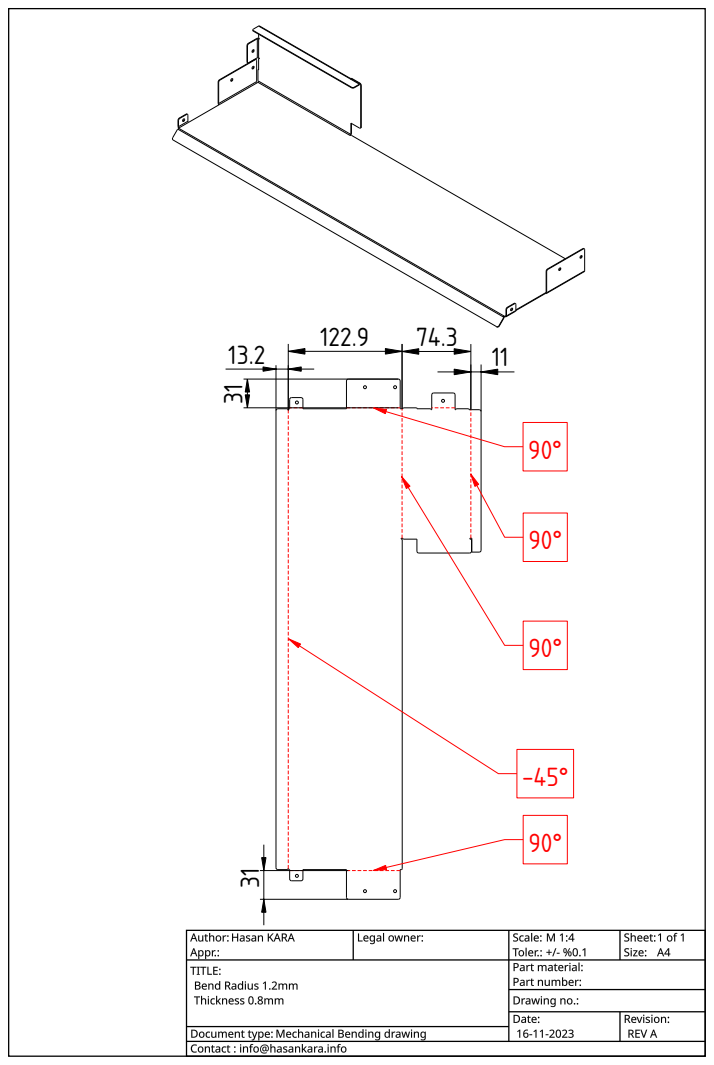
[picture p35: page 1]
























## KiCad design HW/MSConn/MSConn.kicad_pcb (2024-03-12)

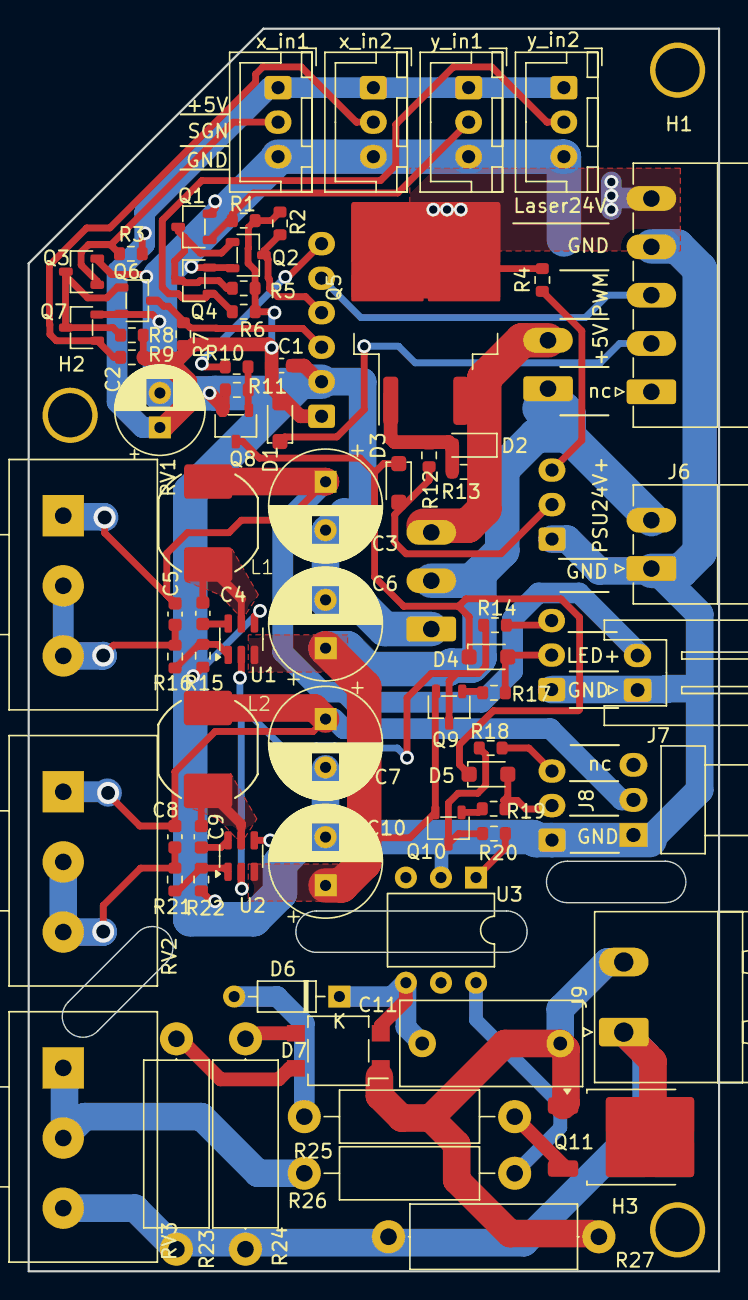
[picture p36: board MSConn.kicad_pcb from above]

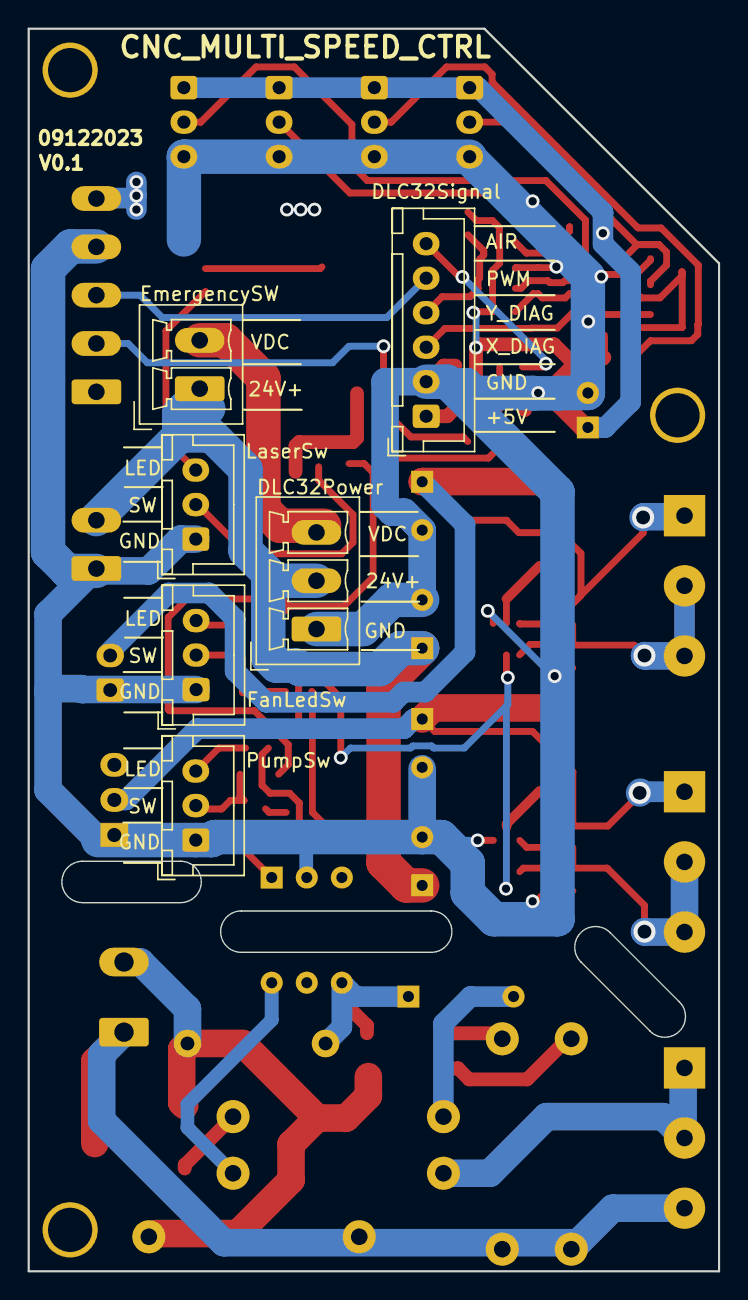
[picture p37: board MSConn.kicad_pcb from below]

Board: 2 copper layers, 50.0 x 90.0 mm, 82 parts (6 on the bottom side), 49 nets.

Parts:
C1, C4, C9: 100nF; C_0603_1608Metric
C2: 220uF 25V; CP_Radial_D6.3mm_H11.0mm_P2.50mm
C3, C6, C7, C10: 220uF 35V; CP_Radial_D8.0mm_H12.0mm_P3.50mm
C5, C8: 47pF; C_0603_1608Metric
C11: 100nF 275Vac; C_Rect_L13.0mm_W6.0mm_P10.00mm_FKS3_FKP3_MKS4
D1, D3, D4, D5: 1N4148; D_SOD-123F-s
D2: MM3Z12; D_SOD-323_HandSoldering
D6: DB3; D_DO-35_SOD27_P7.62mm_Horizontal
D7: MB6S; TO-269AA_spec
H1, H2, H3: M3; MountingHole_3.2mm_M3_DIN965_SmallPad
J1: x_in1; JST_XH_B3B-XH-A_1x03_P2.50mm_Vertical
J2: x_in2; JST_XH_B3B-XH-A_1x03_P2.50mm_Vertical
J3: y_in1; JST_XH_B3B-XH-A_1x03_P2.50mm_Vertical
J4: y_in2; JST_XH_B3B-XH-A_1x03_P2.50mm_Vertical
J5: Laser Terminal; PhoenixContact_MC_1,5_5-G-3.5_1x05_P3.50mm_Horizontal
J6: PSU24V+; PhoenixContact_MC_1,5_2-G-3.5_1x02_P3.50mm_Horizontal
J7: LED+; JST_XH_S2B-XH-A_1x02_P2.50mm_Horizontal
J8: FAN+; FanPinHeader_1x03_P2.54mm_Horizontal
J9: Pump220V; PhoenixContact_MSTBA_2,5_2-G-5,08_1x02_P5.08mm_Horizontal
J10: EmergencySW; PhoenixContact_MCV_1,5_2-G-3.5_1x02_P3.50mm_Vertical
J11: DLC32Signal; JST_XH_B6B-XH-A_1x06_P2.50mm_Vertical
J12: LaserSw; JST_XH_B3B-XH-A_1x03_P2.50mm_Vertical
J13: DLC32Power; PhoenixContact_MCV_1,5_3-G-3.5_1x03_P3.50mm_Vertical
J14: FanLedSw; JST_XH_B3B-XH-A_1x03_P2.50mm_Vertical
J15: PumpSw; JST_XH_B3B-XH-A_1x03_P2.50mm_Vertical
L1, L2: 10uH 3.4A; CD75_Inductor
Q1, Q2, Q3, Q4, Q6, Q7, Q8: PJA3440; SOT-23-3-s
Q5: IRF9540N; TO-263-2-S
Q9, Q10: MMBTA92; SOT-23-3-s
Q11: BTA204S-800E; TO-252-2
R1, R2, R3, R5, R6, R7, R8, R9: 10K; R_0603_1608Metric
R4, R10, R12, R14, R18: 4.7K; R_0603_1608Metric
R11, R13, R17, R19: 100K; R_0603_1608Metric
R15: 750R; R_0603_1608Metric
R16: 12K; R_0603_1608Metric
R20: 2K; R_0603_1608Metric
R21: 3.9K; R_0603_1608Metric
R22: 470R; R_0603_1608Metric
R23, R24: 100K; R_Axial_DIN0414_L11.9mm_D4.5mm_P15.24mm_Horizontal
R25: 1K; R_Axial_DIN0411_L9.9mm_D3.6mm_P15.24mm_Horizontal
R26: 270R; R_Axial_DIN0411_L9.9mm_D3.6mm_P15.24mm_Horizontal
R27: 47K; R_Axial_DIN0414_L11.9mm_D4.5mm_P15.24mm_Horizontal
RV1, RV2: 10K; Potentiometer_Alps_RK163_Single_Horizontal
RV3: 500K; Potentiometer_Alps_RK163_Single_Horizontal
U1, U2: AP63300; TSOT-23-6_SlimPad
U3: MOC3063M; DIP-6_W7.62mm

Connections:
+5V: C1.1, C2.1, D1.2 (A), J1.1, J2.1, J3.1, J4.1, J11.1, R1.1, R2.1, R3.1, R5.1, R6.1, R7.1, R8.1, R9.1
+24V: C6.1, C10.1, J6.2, J10.1, J13.2, Q9.2 (E), Q10.2 (E), U1.3 (IN), U2.3 (IN)
/AC1: J9.1, Q11.2 (A2), R23.2, R24.2, R27.2, RV3.3
/FB: R21.2, R22.2, U2.1 (FB)
/FB1: R15.2, R16.2, U1.1 (FB)
/Fan_Drv: C7.1, C8.1, J8.2, L2.2, RV2.1
/Fan_Led_Btn: D4.2 (A), J14.2, R17.1
/Fan_Led_En: Q9.3 (C), R14.2, U1.2 (EN), U2.2 (EN)
/Laser_Btn: D3.2 (A), J12.2, R12.1
/Laser_Power: J5.5, Q5.2 (S), R4.2
/Led_Drv: C3.1, C5.1, J7.2, L1.2, RV1.1
/Pump_Btn: D5.2 (A), J15.2, R19.1
/Pump_En: Q10.3 (C), R18.2, R20.2
/SGN_AIR: J11.6, R10.2
/SGN_PWM: J5.3, J11.5
/X_DIAG: J11.3, Q6.3 (D), R7.2
/Y_DIAG: J11.4, Q2.3 (D), R2.2
/x_in1: J1.2, Q3.1 (G), R3.2
/x_in2: J2.2, Q7.1 (G), R9.2
/y_in1: J3.2, Q1.1 (G), R1.2
/y_in2: J4.2, Q4.1 (G), R6.2
/~AC1: C11.2, D7.1, J9.2, Q11.1 (A1), R27.1
/~Air: D3.1 (K), D4.1 (K), D5.1 (K), Q8.3 (D)
GND: C1.2, C2.2, C3.2, C6.2, C7.2, C10.2, J1.3, J2.3, J3.3, J4.3, J5.4, J6.1, J7.1, J8.1, J11.2, J12.1, J13.1, J14.1, J15.1, Q1.2 (S), Q2.2 (S), Q3.2 (S), Q4.2 (S), Q6.2 (S), Q7.2 (S), Q8.2 (S), R11.2, R15.1, R22.1, U1.4 (GND), U2.4 (GND), U3.2
unnamed: C5.2, R16.1, RV1.2, RV1.3
unnamed: C8.2, R21.1, RV2.2, RV2.3
unnamed: D1.1 (K), J5.2
unnamed: D2.2 (A), Q5.1 (G), R12.2, R13.2
unnamed: D6.2 (A), R25.1
unnamed: C11.1, D6.1 (K), D7.2, U3.4
unnamed: D7.3 (+), R24.1
unnamed: D7.4 (-), R23.1
unnamed: J12.3, R4.1
unnamed: J14.3, R14.1
unnamed: J15.3, R18.1
unnamed: Q1.3 (D), Q2.1 (G), Q4.3 (D), R5.2
unnamed: Q3.3 (D), Q6.1 (G), Q7.3 (D), R8.2
unnamed: Q8.1 (G), R10.1, R11.1
unnamed: Q9.1 (B), R17.2
unnamed: Q10.1 (B), R19.2
unnamed: Q11.3 (G), R25.2
unnamed: R20.1, U3.1
unnamed: R26.1, RV3.1, RV3.2
unnamed: R26.2, U3.6
unnamed: C4.2, U1.6 (BST)
unnamed: C4.1, L1.1, U1.5 (SW)
unnamed: C9.2, U2.6 (BST)
unnamed: C9.1, L2.1, U2.5 (SW)
VDC: D2.1 (K), J10.2, J13.3, Q5.3 (D), R13.1

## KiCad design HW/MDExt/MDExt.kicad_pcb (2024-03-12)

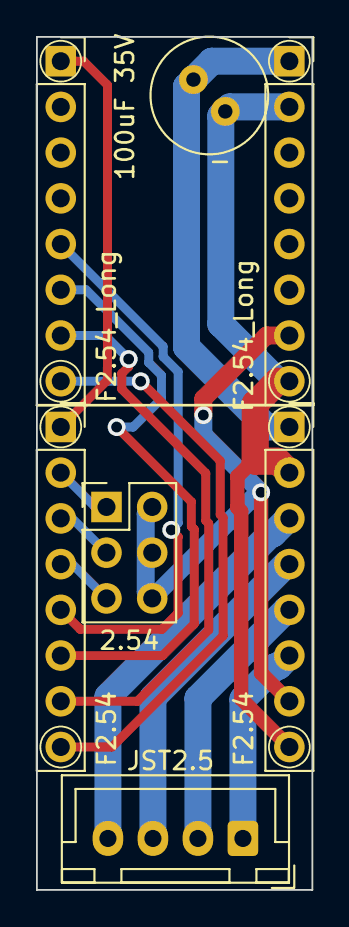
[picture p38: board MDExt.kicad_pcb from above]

Board: 2 copper layers, 15.3 x 47.4 mm, 9 parts (0 on the bottom side), 15 nets.

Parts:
C1: 100uF 35V; C_Radial_D6.3mm_H11.0mm_P2.50mm
J1, J2: F2.54; PinSocket_1x08_P2.54mm_Vertical
J3: 2.54; PinHeader_2x03_P2.54mm_Vertical
J4, J5: F2.54_Long; PinSocket_1x08_P2.54mm_Vertical_Long
J6: JST2.5; JST_XH_B4B-XH-A_1x04_P2.50mm_Vertical
SYM1, SYM2: SYM_TMC2209_3D; Module_TMC2209_3D

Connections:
+5V: J2.7, J3.2, J3.4, J3.6, J5.7
+12V: C1.1, J2.1, J5.1
/MDriverExtendY/DIR: J1.8, J4.8
/MDriverExtendY/EN: J1.1, J4.1
/MDriverExtendY/RST: J1.5, J4.5
/MDriverExtendY/SLP: J1.6, J4.6
/MDriverExtendY/STP: J1.7, J4.7
GND: C1.2, J2.2, J2.8, J5.2, J5.8
unnamed: J1.2, J3.1
unnamed: J1.3, J3.3
unnamed: J1.4, J3.5
unnamed: J2.3, J6.4
unnamed: J2.4, J6.3
unnamed: J2.5, J6.2
unnamed: J2.6, J6.1
